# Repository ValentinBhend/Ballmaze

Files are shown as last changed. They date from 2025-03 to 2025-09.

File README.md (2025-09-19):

# Ballmaze
This project is showcased in this video:

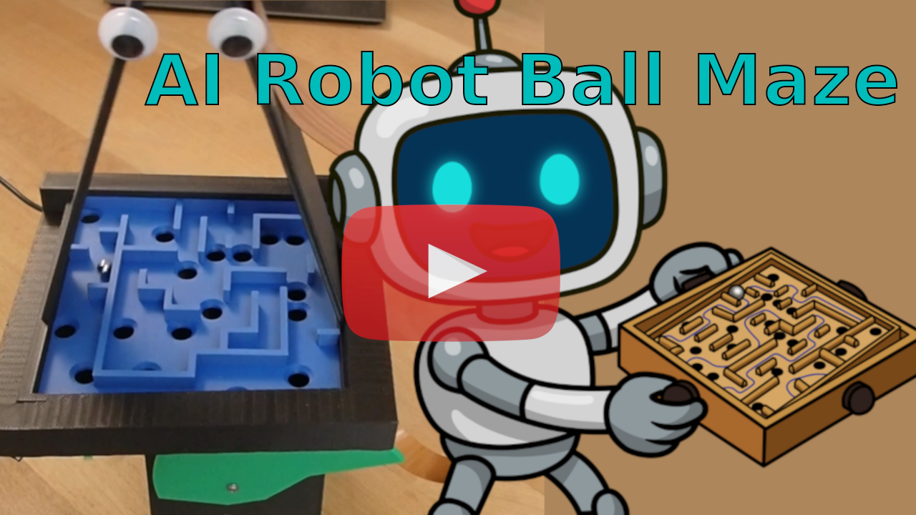
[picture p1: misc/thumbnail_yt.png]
thumbnail_yt (https://www.youtube.com/watch?v=cLjqs_h8txE)


The goal is to automate playing the ballmaze dexterity game. There are quite a few challanges in this and a lot of things can be improved from the current solution. 

<p align="center">
  
  
</p>

This is what it can do currently with roughly 50h of (real-world only) training:

gif_own

## Want to build one yourself?
It's still a work in progress but it works. Some previous experience with a RaspberryPi or similar and a little experience in programming in Python would surely help. And of couse a great interest in robotics/control/machine learning :) <br>
In total the materials cost about 50 - 90 $/€ depending on whether you or someone you know has a 3D printer, or you have to order the 3D printed parts from somewhere. 

### List of materials
Most parts can be replaced by similar ones or whatever you might already have. 

| Part | Price ($/€ approx) | Where to buy |
|---|---|---|
| 1x RaspberryPi Zero 2W (or better)* | 15* | [1](https://www.mouser.ch/ProductDetail/358-SC0721) |
| 2x Servo (e.g. SER0050) | 5 (x2) | [1](https://www.mouser.ch/ProductDetail/426-SER0050) |
| 1x Pi Camera V1.3 | 7 | [1](https://www.mouser.ch/ProductDetail/713-114110127) |
| 1x Pi Camera Cable 300mm | 2 | [1](https://www.mouser.ch/ProductDetail/358-SC1129) |
| 1x uSD card 32GB+ | 5 | [1](https://www.mouser.ch/ProductDetail/358-SC1628) |
| 1x 5V 2A+ USB charger (likely already got one) | 5 | [1](https://www.mouser.ch/ProductDetail/490-SWI10B-5-EW-I38) |
| 1x USB Cable to power Pi (micro USB for Pi Zero)  | 2 | [1](https://www.mouser.ch/ProductDetail/530-SC-2AMK003F) |
| A few metal balls with diameter ~6mm | 5 | [1](https://www.amazon.com/0-236-Precision-Chrome-Steel-Bearing/dp/B07L8MLK2N) |
| 3D printed Parts (~300g PLA/PETG) | 5 - 40 | ... |
| Some cables + soldering iron would be<br>useful to connect the servos (not required) | |  |
| 2x Googly eyes (strictly required) | |  |

*The latest version used a RaspberryPi 5 which is about 80€ with a cooler. But I'm working on getting it as fast on the Pi Zero. 

*If you built this, please send me a link to where you bought the parts, so I can add them to the table.*

### Physical setup
... some pictures & stuff ...

### Setup on the PC
To get the code on your PC running, first download the repo as a .zip and unpack, or clone it to a local folder. <br>
There are requirements.txt files in the respective folders. Those were generated with Python 3.12.3, so might not work exactly the same for other versions. <br>
To execute the Python scripts and try the algorithms provided here, first set up a Python virtual environment (venv) in each of the folders which contain python files. <br>
In a Linux terminal it would be: <br>
if not installed: `sudo apt install python3-venv` <br>
`cd Code_on_PC/` or other folders <br>
`python3 -m venv .venv` creates the virtual environment<br>
`source .venv/bin/activate` activates the venv (has to be executed again after you open a new terminal later on)<br>
`pip install -r requirements.txt` installs the list of packages<br>
 for Windows/Mac it is similar, see here [docs.python.org/3/library/venv.html](https://docs.python.org/3/library/venv.html) <br>
Alternatively you can also install the Python packages manually.

### RaspberryPi setup
I used a RaspberryPi but any other single-board computer should work if it has these features: <br>
- 2 Hardware PWMs to control the servos. (Software PWMs, at least on my Pi, don't work for servos under load)
- Connection to the camera (Picam Zero v1.3 in my case)
- Connection to a PC (preferrably wired to reduce lag, alternatively SSH over local Wi-Fi)

A good tutorial to set up a RaspberryPi with PiOS to then communicate to your PC over your local Wi-Fi via SSH can be found here: [randomnerdtutorials.com/installing-raspbian-lite-enabling-and-connecting-with-ssh](https://randomnerdtutorials.com/installing-raspbian-lite-enabling-and-connecting-with-ssh/) (Skip steps 3 & 4 by already doing them in step 2 as it says. )<br>

I first used a the slower RaspberryPi Zero 2W and later switched to the RaspberryPi 5 because the image detection was too slow. I used a moderately sized deep-learning model to detect the ball. It should be possible to get it to work on the smaller & cheaper Pi Zero with a simpler and lighter detection-algorithm though. On the Pi Zero, the setup is a bit weird because of the out-of-date PiCamera package. So I'll describe the setups seperately:

<table>
  <tr>
    <td valign="top" width="50%">

### Pi Zero 2W setup
Here I have chosen the `Legacy 64-bit Lite` (Debian GNU/Linux 11) version in the Pi Imager shown in the above linked tutorial. <br>
- Open a SSH terminal on the Pi and check the OS version with the command:
```bash
uname -m
```
this should show: `aarch64`. If it shows `armv7l` you choose the 32bit version which will not work, rewrite the image onto the SD card with the 64bit version.<br>
Then run:
```bash
cat /etc/os-release
```
This should show: (if not, the wrong version might have been selected in the Pi Imager)
```plaintext
PRETTY_NAME="Debian GNU/Linux 11 (bullseye)"
NAME="Debian GNU/Linux"
VERSION_ID="11"
VERSION="11 (bullseye)"
VERSION_CODENAME=bullseye
ID=debian
HOME_URL="https://www.debian.org/"
SUPPORT_URL="https://www.debian.org/support"
BUG_REPORT_URL="https://bugs.debian.org/"
```
- Also on the Pi, run the commands: (takes a rew minutes)
```bash
sudo apt update
sudo apt -y upgrade
sudo apt install -y libgl1
sudo sed -i \
  '1i\
# enables hardware PWM on pins GPIO_18, GPIO_19 (Pins 12, 35)\
dtoverlay=pwm-2chan\
# limits camera memory to 320MB, not required on e.g. a Pi 4/5\
dtoverlay=vc4-kms-v3d,cma-320' \
  /boot/config.txt
sudo reboot
```

Once you can connect to the Pi over the terminal, follow these steps: <br>

This restarts the Pi, connect to it again. 
- Download this git repo to your PC (if not already done).
- Copy the folder **Code_on_RaspberryPi** the the /home/USER directory on the Pi.<br>
  USER and DEVICE are whatever you called them in the Pi imager, USER is `pi` by default.<br>
  For this open a <ins>**termina/Powershell on your PC**</ins> and run:<br>
```bash
scp -r path/on/your/PC/to/the/folder/Code_on_RaspberryPi \
USER@DEVICE.local:/home/USER
```
Alternatively you can also copy the folder onto the SD card. 
- Now back to the Pi SSH terminal, check if it has the `Code_on_RaspberryPi` folder by:
```bash
ls
```
this should show the folder: `Code_on_RaspberryPi`
- Run these commands still in the current (`home/pi`) directory:
```bash
sudo apt install -y python3-picamera2 --no-install-recommends
sudo apt install -y python3-venv
cd Code_on_RaspberryPi
python3 -m venv --system-site-packages .venv
source .venv/bin/activate
pip install --upgrade pip
pip install openvino==2025.0.0 opencv-python==4.11.0.86 \
zmq==0.0.0 rpi_hardware_pwm==0.2.2 scipy==1.10.1 numpy==1.19.5
pip install numpy==1.19.5 scikit-optimize==0.9.0
```

  </td>
  <td valign="top" width="50%">

### Pi 5 setup
Here I have chosen the newest 64bit Pi OS with a GUI (Debian GNU/Linux 12) version in the Pi Imager shown in the above linked tutorial. The headless version would need manual installation of the camera driver, but the Pi 5 is fast enough to handle the unused GUI in the background.<br>
- Open a SSH terminal on the Pi and check the OS version with the command:
```bash
uname -m
```
this should show: `...`. If it shows `...` you choose the 32bit version which will not work, rewrite the image onto the SD card with the 64bit version.<br>
Then run:
```bash
cat /etc/os-release
```
This should show: (if not, the wrong version might have been selected in the Pi Imager)
```plaintext
TODO...
```

- Also on the Pi, run the commands: (takes a rew minutes)
```bash
sudo apt update
sudo apt -y upgrade
sudo sed -i \
  '1i\
# enables hardware PWM on pins GPIO_18, GPIO_19 (Pins 12, 35)\
dtoverlay=pwm-2chan\
  /boot/config.txt
sudo reboot
```

Once you can connect to the Pi over the terminal, follow these steps: <br>

This restarts the Pi, connect to it again. 
- Download this git repo to your PC (if not already done).
- Copy the folder **Code_on_RaspberryPi** the the /home/USER directory on the Pi.<br>
  USER and DEVICE are whatever you called them in the Pi imager, USER is `pi` by default.<br>
  For this open a <ins>**termina/Powershell on your PC**</ins> and run:<br>
```bash
scp -r path/on/your/PC/to/the/folder/Code_on_RaspberryPi \
USER@DEVICE.local:/home/USER
```
Alternatively you can also copy the folder onto the SD card. 
- Now back to the Pi SSH terminal, check if it has the `Code_on_RaspberryPi` folder by:
```bash
ls
```
this should show the folder: `Code_on_RaspberryPi`
- Run these commands still in the current (`home/pi`) directory:
```bash
sudo apt install -y python3-picamera2
sudo apt install -y python3-venv
cd Code_on_RaspberryPi
python3 -m venv .venv
source .venv/bin/activate
pip install --upgrade pip
pip install openvino opencv-python zmq \
rpi_hardware_pwm scipy numpy scikit-optimize
```

  </td>
  </tr>
</table>

It now shows `(.venv)` at the start of the line in the terminal, which indicated the venv is running ([Read more about venv](https://docs.python.org/3/library/venv.html)). Whenever you open a new terminal, go to the Code-folder with `cd Code_on_RaspberryPi` and activate the venv with `source .venv/bin/activate`. 
- Run this Python script to check the installation:
```bash
python3 check_installation.py
```
It if gives any errors, read it and try re-running the installation commands it might correspond to. 

### Check setup
*TODO, not implemented: Now slide the empty-maze-plate in and put a metal ball on it. Then run the script `python3 check_everything_PC.py` on the PC together with `python3 check_everything_Pi.py` on the Pi while connected to the same Wi-Fi.*

When the check was succesfull, run `python3 pi_calibration.py` on RaspberryPi with the empty-maze-plate still inserted. <br>
It is recommended to run `pi_calibration.py` before every session. It measures the relative position of the camera and adjusts it for lighting conditions. 

## Further plans
- Write a simulation to pretrain a model.
- Pretrain the CNN as part of an autoencoder.
- Make a proper hyperparameter sweep, including the reward-structure.
- Use (implicit) meta-learning to train on different maze layouts and/or with different builds (an algorithm trained on one build/setup might not work on another because of slight imprecisions).
- Cut some costs: Smaller servo motors, cheaper camera, working (faster) Pi Zero setup, ... -> Then build more of them to train in parallel.
- Make some more games in the same style and reuse most of the hardware.

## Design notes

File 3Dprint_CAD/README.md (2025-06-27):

Everything was designed in OpenSCAD which is a free CAD-software which is script-based. <br>
I printed everything on a Bambu Lab P1S 3D printer with PLA. Earlier version were also made on a Prusa MK3S with PLA and PETG. 

The .scad source file scripts have gotten really messy over time. So if you want to costumize something, brace yourself. 

The printplates are also available as .3mf files here. 

### Some remarks on the different models:

**CLIP**: This is a slightly modified version of the part "Clip-On-2DOF-Joint (no torsion)" shared by the user "mechadense" on thingyverse: [thingiverse.com/thing:5533090](https://www.thingiverse.com/thing:5533090). It us licenced under the [Attribution-ShareAlike 3.0 Unported](https://creativecommons.org/licenses/by-sa/3.0/) licence and therefore also my version is. <br>
It is great, it enables tilting the maze without allowing it to rotate. 

**HOLDER**: This is the only part with sketchy overhangs and a lot of bridges. It might be safer to print the camera-holder-triangle on top seperately and in a different orientation, then glue it on. But it has worked for me as a single part. <br>
The camera is a bit hard to get in and might require a knife. This could be improved..

**MAZE**: The maze is best printed with ironing enabled on top-surfaces for a smooth surface (might need advanced/expert options enabled). <br>
There is an empty maze without holes which can be useful for testing or learning the exact dynamics of the system. <br>
The maze layout can be modified with the lists "hole_coords, wall_coords_h, wall_coords_v and corner_coords" in the config.scad file

**all.scad** this shows the whole thing, don't try to print it :)

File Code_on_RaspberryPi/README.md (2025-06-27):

How to set up the RaspberryPi is described in the [main README.md](https://github.com/ValentinBhend/Ballmaze/blob/main/README.md#raspberrypi-setup) <br>

**Some remarks**
- To setup the RaspberryPi, SSH over a local Wi-Fi is somewhat convenient. But I had lags of up to 200ms, so I switched to a wired connection (ethernet) later on. 
- On a RaspberryPi Zero, the camera port / CSI slot is very fragile. After breaking two, I glued the cable into the port. I might try designing a 3D printed part to make it more robust.

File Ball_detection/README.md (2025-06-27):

The Ball detection in being done with the YOLO11n algorithm using the user friendly Ultralytics implementation in Python. 

The current pytorch (.pt) model and exported OpenVINO model are already trained. The OpenVINO model is the folder of the other Pi scripts in this project. <br>
To train it differently or with another dataset, the whole trianing and exporting procedure is in YOLO_train_export.ipynb which can also be ran on Google Colab. 

There are currently ~2000 labeled images with a ball and another ~3000 empty images. <br>
The labeled dataset can be found at: [kaggle.com/datasets/valentinbhend/ballmaze-labeled-images](https://www.kaggle.com/datasets/valentinbhend/ballmaze-labeled-images) <br>
The labels are axis-aligned bounding boxes of the metal ball and were made using Label Studio.

On the RaspberryPi5, there will be a memory over unless you use the line:
```ie.set_property("CPU", {"INFERENCE_NUM_THREADS": 1, "NUM_STREAMS": "1"})```
I reported this issue, no idea why this is happening.

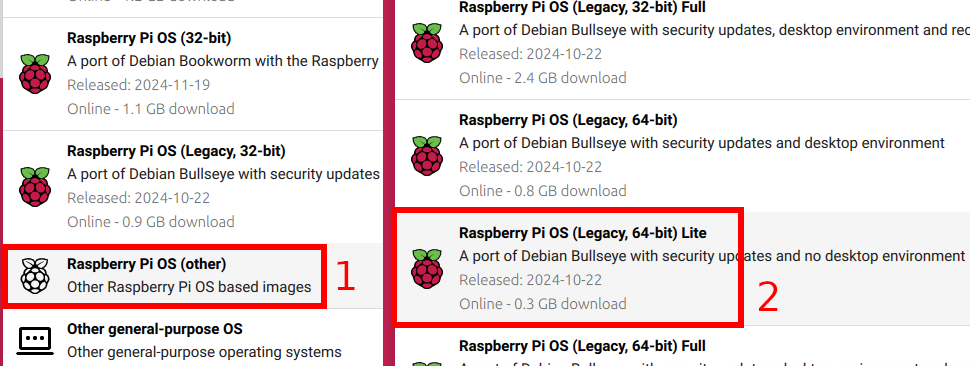
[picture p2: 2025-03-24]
misc/PiOS_selection.png

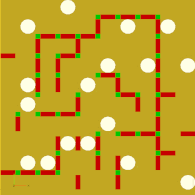
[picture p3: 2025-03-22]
Code_on_PC/maze1.png

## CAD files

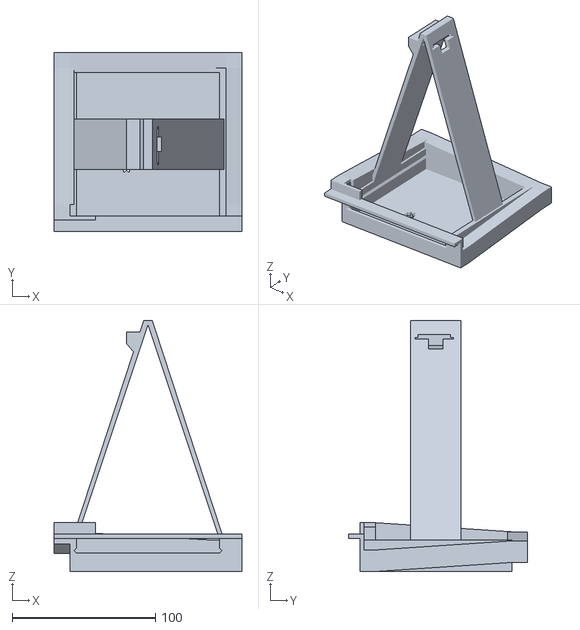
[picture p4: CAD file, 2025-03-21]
3Dprint_CAD/STL_files/HOLDER_x1.stl
131.0 x 125.0 x 175.0

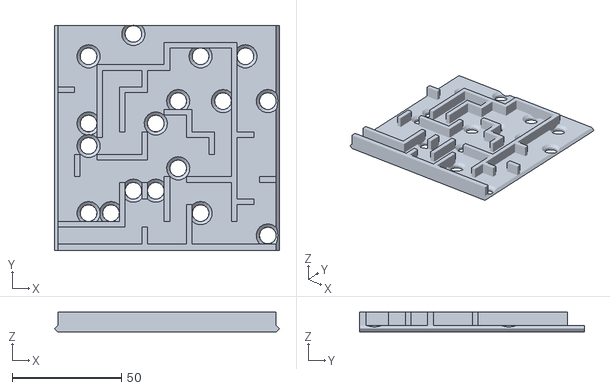
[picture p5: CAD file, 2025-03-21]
3Dprint_CAD/STL_files/MAZE1_x1.stl
103.0 x 103.0 x 9.00

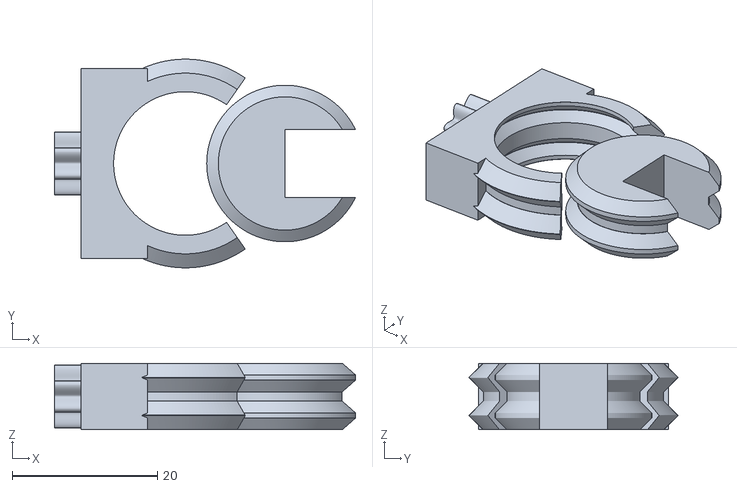
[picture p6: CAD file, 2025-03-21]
3Dprint_CAD/STL_files/CLIP_x2.stl
41.4 x 28.7 x 9.13

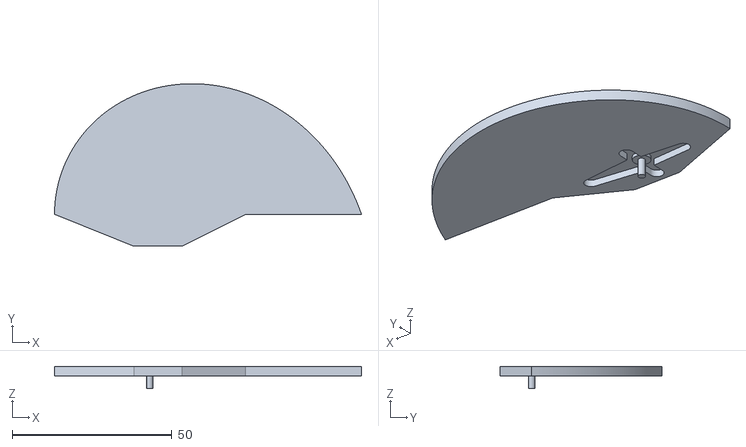
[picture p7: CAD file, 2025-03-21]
3Dprint_CAD/STL_files/ARM_x2.stl
96.0 x 50.8 x 7.00

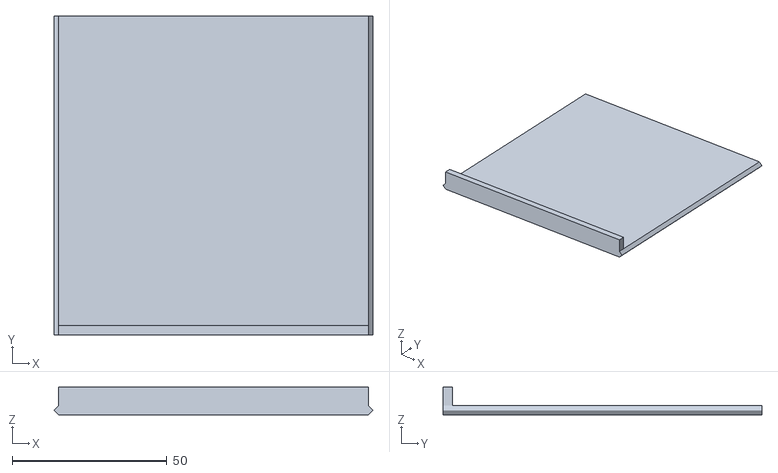
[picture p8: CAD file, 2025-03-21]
3Dprint_CAD/STL_files/MAZEempty_x1.stl
103.0 x 103.0 x 9.00

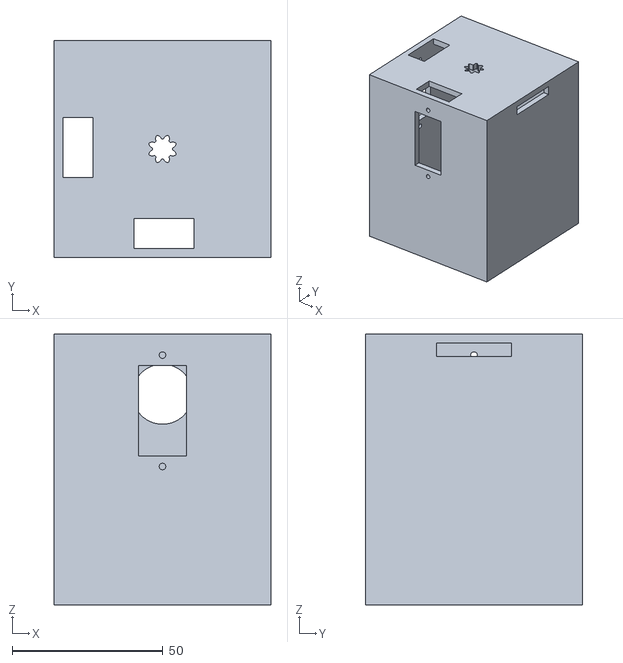
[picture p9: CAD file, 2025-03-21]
3Dprint_CAD/STL_files/BOX_x1.stl
72.0 x 72.0 x 90.0

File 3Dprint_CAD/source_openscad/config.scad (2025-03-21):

plate_sidelength = 100;
//hole_radius = 25/6;
gridsize = plate_sidelength/(4*10-1);
plate_thickness = 3;
bot_plate_maze_space = 10;
wall_height = 6;
hole_out_r = 4;
slide_width = 8;
camera_height = 150;
holder_wall_width = 35;
camera_width = 10;
fn = 100;

box_height = 90; // change
box_shift = 0;
box_width = 72;
box_width1 = box_width + box_shift;
servo_h_offset = 18; // change
h_clip = 30; // change
max_angle = 20;
w_arm = 17 - plate_thickness;
w_arm_full = w_arm + box_width/2;
pivot_offset = 15; // 0 would be in the middle

clip_cutout_w = 2;
clip_scale = 46/h_clip;


hole_coords = [[0,0], [6,0], [8,1], [6,2], [1,3], [3,4], [6,4], [2,5], [5,5], [2,6], [9,6], [1,7], [4,8], [8,8], [1,8], [5,8], [8,3]];
wall_coords_h = [[0,3], [0,5], [1,1], [1,3], [1,4], [1,6], [2,1], [2,4], [2,5], [2,6], [3,1], [3,8], [4,1], [4,2], [4,5], [5,1], [5,3], [5,7], [6,1], [6,7], [7,1], [7,7], [8,1], [8,4], [5,6], [6,6], [7,5]];
wall_coords_v = [[0,7], [0,8], [0,9], [1,1], [2,0], [2,2], [2,3], [3,6], [3,7], [4,3], [5,4], [7,5], [7,6], [7,7], [8,2], [8,3], [8,4], [6,9], [4,1], [6,6]];
corner_coords = [[0,3], [0,6], [0,7], [0,8], [1,1], [1,4], [1,6], [2,1], [2,2], [2,3], [3,1], [3,5], [3,6], [3,8], [4,1], [4,2], [4,3], [5,1], [5,3], [5,7], [6,1], [6,7], [7,1], [7,4], [7,5], [7,6], [7,7], [8,1], [8,2], [8,3], [8,4], [2,4], [3,7], [4,5], [5,4], [4,7], [6,5], [6,6], [5,6]];

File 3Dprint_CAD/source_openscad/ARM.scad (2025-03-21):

include <config.scad>;
use <arm_servo_cutout.scad>;

function r(turn_angle) = 
    let (
        tilt_angle = -max_angle 
        + 2*max_angle*turn_angle/180,
        H = h_clip + servo_h_offset
    )
    H - w_arm_full * tan(tilt_angle);


function r1(turn_angle) = 
    let (
        tilt_angle = -max_angle 
        + 2*max_angle*turn_angle/180,
        H = h_clip + servo_h_offset,
        h1 = H + w_arm_full * tan(max_angle),
        h2 = H - w_arm_full * tan(max_angle)
    )
    h2 + (h1-h2) * (180-turn_angle)^2 / 180^2;


module spiral(){
    H = h_clip + servo_h_offset;
    h1 = H + w_arm_full * tan(max_angle);
    h2 = H - w_arm_full * tan(max_angle);
    d = plate_thickness;
    points = [for (i=[0:180]) [r1(i)*cos(i), r1(i)*sin(i)]];
    linear_extrude(d)
    polygon(points);
}

module arm(){
    d = plate_thickness;
    difference(){
        union(){
            spiral();
            linear_extrude(d)
            polygon([[-r(180),0], [-5,-10], 
                     [10,-10], [30,0], [r(0),0]]);
        }
        rotate(180)
        servo_cutout();
    }
    servo_pin_extension();
}

arm();

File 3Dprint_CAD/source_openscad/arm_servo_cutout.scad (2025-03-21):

d1 = 17;
d = 4;
m1 = 8;
m2 = 6;
l1 = 17;
l2 = 14;
fn = 50;

module L(){
    union(){
        polygon([[0,-m1/2], [0,m1/2], 
                 [-l1,d/2], [-l1,-d/2]]);
        translate([-l1,0])
        circle(d/2, $fn=fn);
    }
}
module R(){
    union(){
        polygon([[0,-m2/2], [0,m2/2], 
                [l2,d/2], [l2,-d/2]]);
        translate([l2,0])
        circle(d/2, $fn=fn);
    }
}
module M(){
    l = d1-d;
    union(){
        polygon([[d/2,-l/2], [d/2,l/2], 
                 [-d/2,l/2], [-d/2,-l/2]]);
        translate([0,l/2])
        circle(d/2, $fn=fn);
        translate([0,-l/2])
        circle(d/2, $fn=fn);
    }
}

module servo_cutout(){
    difference(){
        linear_extrude(2){
            L();
            R();
            M();
        }
        union(){
            translate([0,0,1])
            linear_extrude(2){
                circle(2.5, $fn=fn);
            }
            translate([0,0,0])
            linear_extrude(1){
                circle(1, $fn=fn);
            }
        }
    }
}



module servo_pin_extension(){
    h_pin = 4;
    translate([0,0,-h_pin])
    cylinder(h_pin,1, $fn=fn);
}

servo_cutout();
servo_pin_extension();

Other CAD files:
3Dprint_CAD/3MF_printplates/Printplate2.gcode.3mf
3Dprint_CAD/3MF_printplates/Printplate1_Mazes_with_ironing.gcode.3mf
3Dprint_CAD/source_openscad/all.scad
3Dprint_CAD/STL_files/HOLDER.scad
3Dprint_CAD/source_openscad/BOX.scad
3Dprint_CAD/source_openscad/CLIP.scad
3Dprint_CAD/source_openscad/MAZE.scad
3Dprint_CAD/source_openscad/clip_Tracta2022_mechadense.scad
3Dprint_CAD/source_openscad/holder_bot_plate.scad
3Dprint_CAD/source_openscad/holder_camera_arch.scad
3Dprint_CAD/source_openscad/picam_slot.scad

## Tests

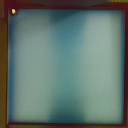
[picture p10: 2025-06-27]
Code_on_RaspberryPi/test_img.png

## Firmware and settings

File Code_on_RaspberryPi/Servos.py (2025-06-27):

from rpi_hardware_pwm import HardwarePWM
import time
from threading import Thread

class Servos:
    def __init__(self, mode="50hz"):
        self.mode = mode
        if mode=="50hz":
            self.pwm1 = HardwarePWM(pwm_channel=0, hz=50, chip=0)
            self.pwm2 = HardwarePWM(pwm_channel=1, hz=50, chip=0)
            self.v0, self.v1 = 6, 11
        elif mode=="100hz":
            self.pwm1 = HardwarePWM(pwm_channel=0, hz=100, chip=0)
            self.pwm2 = HardwarePWM(pwm_channel=1, hz=100, chip=0)
            self.v0, self.v1 = 12, 22
        else:
            assert False, f"invalid mode: {mode}"
        self.pwm1.start(2)
        self.pwm2.start(2)
        self.x = -0.5
        self.y = -0.5
        self.set(self.x, self.y)
        time.sleep(1)
    
    def set(self,x,y):
        assert (x<=1 and x>=-1 and y<=1 and y>=-1), "set x,y between -1 and 1"
        dc1 = (self.v1-self.v0)*0.5*x + (self.v1+self.v0)*0.5
        dc2 = (self.v1-self.v0)*0.5*y + (self.v1+self.v0)*0.5
        self.pwm1.change_duty_cycle(dc1)
        self.pwm2.change_duty_cycle(dc2)
    
    def smooth_blocking_pizero(self, x1, y1, speed=1):
        x0 = self.x
        y0 = self.y
        T = 0.5 / speed
        N_steps = int(T/T_step)
        for i in range(1, N_steps+1):
            t_start = time.monotonic()
            x = x0 + (x1 - x0) * (i / N_steps)
            y = y0 + (y1 - y0) * (i / N_steps)
            self.set(x, y)
            elapsed = time.monotonic() - t_start
            time.sleep(max(0, T_step - elapsed))
        self.x = x
        self.y = y
    
    def smooth_blocking(self, x1, y1, speed=1):
        x0 = self.x
        y0 = self.y
        T = 0.5 / speed
        if self.mode == "50hz":
            T_step = 0.02
        elif self.mode == "100hz":
            T_step = 0.01
        N_steps = int(T/T_step)
        assert N_steps>0, "speed too fast for servos"
        for i in range(1, N_steps+1):
            t_start = time.monotonic()
            x = x0 + (x1 - x0) * (i / N_steps)
            y = y0 + (y1 - y0) * (i / N_steps)
            self.set(x, y)
            elapsed = time.monotonic() - t_start
            time.sleep(max(0, T_step - elapsed))
        self.x = x
        self.y = y

    def smooth(self,x1,y1,speed=1):
        thread = Thread(target=self.smooth_blocking, args=(x1, y1, speed))
        thread.start()
        return thread

    def stop(self):
        self.smooth(-0.5, -0.5)
        self.pwm1.stop()
        self.pwm2.stop()

    def temp_play(self):
        #self.reset()
        self.smooth(0.45,0.82,speed=0.2)
        time.sleep(0.2)
        self.smooth(0.45,0.45,speed=1)
        self.smooth(0.45,0.82,speed=1)
        time.sleep(0.4)
        self.smooth(0.45,0.65,speed=0.5)
        time.sleep(0.8)
        self.smooth(0.7,0.82,speed=0.8)
        self.smooth(0.45,0.45,speed=0.5)
        time.sleep(0.5)
        self.smooth(0.82,0.45,speed=0.5)
        time.sleep(0.2)
        self.smooth(0.45,0.82,speed=0.5)
        time.sleep(0.2)

if __name__ == "__main__":
    def check_smoothness_range(servos):
        speeds = [0.5, 1, 2, 3, 4, 5]
        for speed in speeds:
            print(f"speed: {speed}")
            servos.smooth_blocking(-1,-1)
            servos.smooth_blocking(1,1)

    x,y = 0,0

    servos = Servos()
    servos.set(x,y)
    print("50hz set")
    #del servos
    time.sleep(2)
    servos = Servos(mode="100hz")
    servos.set(x,y)
    print("100hz set")
    time.sleep(2)

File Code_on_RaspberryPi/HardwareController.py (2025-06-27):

import pickle
import numpy as np
import cv2
from Camera import Camera
from Servos import Servos
from Detector import Detector
import time
import subprocess


class HardwareController:
    calibration_filename = "PiCalibration.pkl"
    def __init__(self):
        with open(self.calibration_filename, "rb") as f:
            self.calibration = pickle.load(f)
        self.camera = Camera(
            AnalogueGain = self.calibration["AnalogueGain"], 
            ExposureTime = self.calibration["ExposureTime"])
        self.servos = Servos(mode="100hz")
        self.detector = Detector()

        offset = 3/101 + 1/101 # r_ball + wall at the side
        pts_dst = np.array([
            [offset, offset],      # point a'
            [offset, 1-offset], # TODO: check if BR & TL switched
            [1-offset, 1-offset],      # point c'
            [1-offset, offset]       # point d'
        ], dtype=np.float32)
        pts_src = self.calibration["image_corners"]
        self.position_transform_matrix = cv2.getPerspectiveTransform(pts_src, pts_dst)
        servo_setpoints = self.calibration["servo_setpoints"]
        target = np.array([[-1.0,-1.0], [-1.0,1.0], [1.0,1.0], [1.0,-1.0]], dtype=np.float32)
        self.setpoint_transform_matrix = cv2.getPerspectiveTransform(target, servo_setpoints)
        #self.detector_reset_count = 0

    def tests(self):
        setpoint = np.zeros(2).astype(np.float32)
        for _ in range(200):
            thread = self.move_servo(*setpoint, speed=3)
            position = None
            while position is None:
                position = self.get_position()
            setpoint -= 0.05 * position
            setpoint = np.clip(setpoint, -1.0, 1.0)

    def move_servo(self,x,y,speed=1):
        points_in = np.array([[[x,y]]], dtype=np.float32)
        setpoints = cv2.perspectiveTransform(points_in, self.setpoint_transform_matrix)[0,0]
        return self.servos.smooth(*setpoints, speed=speed)

    def move_servo_blocking(self,x,y,speed=1):
        thread = self.move_servo(x, y, speed=speed)
        thread.join()

    def get_position(self, conf=0.001, save=False):
        #self.detector_reset_count += 1
        #if self.detector_reset_count > 1000:
        #    self.detector = init_free_Detector(Det=self.detector)
        #    self.detector_reset_count = 0
        #T = self.get_cpu_temp()
        #if T > 65:
        #    print(f"\33[31mCPU overheating during play: {T}>65\33[0m")
        #    time.sleep(1)
        #print(T)

        arr = self.camera.capture_np(save=save)
        xywhn = self.detector.get_xywhn(arr, conf=conf)
        if xywhn is None:
            print("no detect!")
            return None
        position_camera = xywhn[:2].reshape(1, 1, 2)
        position_transformed = cv2.perspectiveTransform(position_camera, self.position_transform_matrix)[0,0]
        return position_transformed*2-1

    def reset_special_solve(self):
        A = [[1,-1]]
        B = [[-1,-1]]
        C = [[1,1]]
        D = [[-1,1]]
        reset_actions = np.array(
            B*10+
            A*5+
            B*5+
            D*5+
            B*5+
            D*5+
            C*10+
            D*5+
            C*5+
            D*10+
            B*5+
            A*5+
            B*10+
            A*5+
            C*5+
            A*5+
            B*8+
            A*5+
            C*5+
            A*5+
            C*10+
            D*10+
            B*5+
            A*5+
            B*10+
            D*10+
            C*10
            )
        position = 0
        while position is not None:
            for act in reset_actions:
                self.move_servo_blocking(*act, speed=3.5)
            position = self.get_position(conf=0.02)

    def reset(self):
        #self.detector = init_free_Detector(Det=self.detector)
        #self.detector_reset_count = 0
        #self.reset_special_solve() ############ ONLY FOR THE MAZE WITH NO HOLES!! comment out otherwise
        position = None
        while position is None:
            print("starting reset")
            self.servos.smooth_blocking(0.5,0.5,speed=0.5)
            time.sleep(0.5)
            self.servos.smooth_blocking(0.7,-1,speed=0.8)
            time.sleep(1)
            self.servos.smooth_blocking(-1,-1,speed=2)
            time.sleep(1)
            self.servos.smooth_blocking(-1,0.7,speed=1)
            time.sleep(1)
            self.servos.smooth_blocking(0.7,0.7,speed=0.5)
            time.sleep(1)
            self.move_servo_blocking(1,-1,speed=1)
            time.sleep(0.2)
            self.move_servo_blocking(1,1,speed=1.5)
            time.sleep(0.2)
            self.move_servo_blocking(0,0,speed=1)
            time.sleep(1)

            position = self.get_position(conf=0.05)
        #T = self.get_cpu_temp()
        #while T>60:
        #    print(f"\33[31mCPU temp too high after reset: {T}>60\33[0m")
        #    time.sleep(2)
        #    T = self.get_cpu_temp()
        #print(f"CPU temp: {T}")
        return position

    def get_image(self): # only for debugging
        raise NotImplementedError
        return np.zeros((128,128,3))
    
    @staticmethod
    def get_cpu_temp():
        output = subprocess.check_output(["vcgencmd", "measure_temp"]).decode()
        temp_str = output.split('=')[1].split("'")[0]
        return float(temp_str)


if __name__ == "__main__":
    HC = HardwareController()
    HC.reset()

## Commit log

2025-06-27 Fixed the mirrored camera holder
    [HOLDER.scad]
2025-06-27 Updated Holder CAD file
    [Printplate1_Mazes_with_ironing.3mf, Printplate1_Mazes_with_ironing.gcode.3mf, Printplate2.3mf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]
